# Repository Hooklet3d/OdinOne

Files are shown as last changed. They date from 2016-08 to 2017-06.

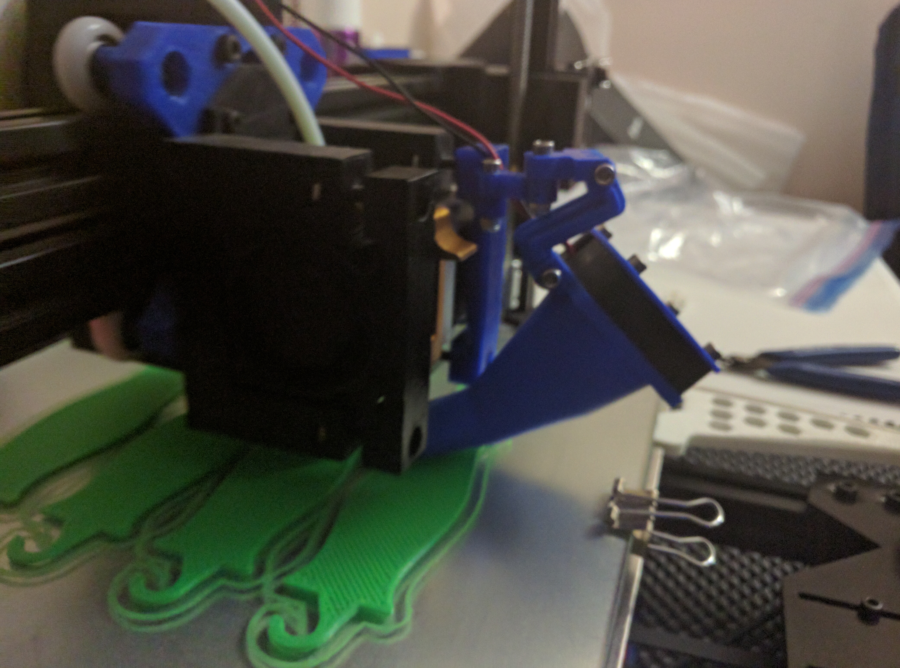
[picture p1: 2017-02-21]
Parts/OdinOne/Mods/Mk1Cooler/LayoutExample2.jpg

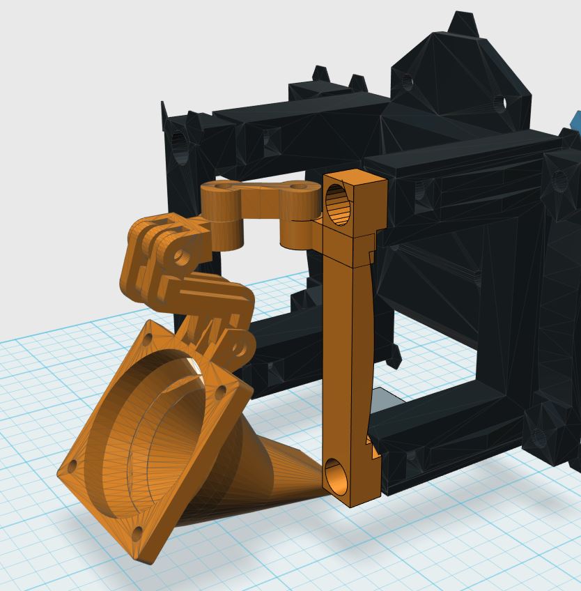
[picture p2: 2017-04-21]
Parts/OdinOne/Mods/Active_Cooling/Mk8CoolerModular/ModLayout.JPG

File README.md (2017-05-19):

# Odin One 3d Printer

Published under GPL v3

## About

This repository contains the files needed to print and assemble the 3d printed parts of the Odin One 3d printer.  As the machine is modified this repository will be updated to reflect the most current revision.  

Each folder contains a text file with basic information on how to configure and print these parts.  Please reference the build manual for specific information on assembly.  

A primary goal of the Odin One is the create a high quality teaching tool.  Contributing to 3d printing eduction for the public is very important to us.  With that said, please share your contributions and findings with the community. 

## What's New

## May 2017

* Work continues on improving the included cooling solution (duct), currently the duct is effective but we do have some room to improve.  
* The team is focusing on producing kits and as we move into the summer show tour
* It's time to start looking into ways of improving the extruder solution and the x-axis; a key point of improvement is weight reduction.
* We are looking at making big improvements to the MK8 extruder as well, more on that to come!
* The current controller case solution is being updated and improved as of now. 

### May 19 2017

PR: Mercury 1 (PR#66)
*	Reworked Unicap’s to tighten tolerances and reduce weight
*	Fixed an alignment issue with the Bed Belt Mount
*	Reworked Y Idle Mount
*	Reworked Y NEMA Mount for better fit
*	Reworked MK8 Mount for better alignment and strength 

#### April 2017
All MK1 parts have been uploaded to the master branch.
The WIKI is slowly being updated with info and specific guides

### What's Next

Moving forward we will be focusing on improving documentation (to include BOM) and including CAD files for all parts.

Currectly the Odin CAD files are SKP (Sketchup) we will be reworking and sharing Fusion360 files for all items.

### TODO

We need to verify and update the documentation (this includes markup on existing .MD files)

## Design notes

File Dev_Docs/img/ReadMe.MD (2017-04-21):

# Docs Needed

## Guide Docs

* Belt Adjust
* Setting Z-Offset

## Build Docs

* Machine Verification
* Fan Wiring

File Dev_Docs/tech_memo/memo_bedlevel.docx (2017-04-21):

Hooklet3D
Odin One Development

Monticello, MN 55362

MEMORANDUM

Date: March 27, 2017

To: Community

From: Hooklet Development Team

Subject: Manual Bed Level

Summary: The Odin One MK1 is equipped with an auto bed level (ABL) system, this does not mean there’s no need to level the bed, however, it does limit the frequency it must be leveled. The addition of the ABL system slightly alters the process of leveling the bed. This document will outline the steps needed to physically level the build surface.

Process:

Step 1-

Tighten the bed thumbscrews compressing the bedsprings to approximately half their extended length

Step 2-

Auto home the machine using either the LCD or Gcode and then perform an auto bed level:

LCD: Prepare/Auto Home

Code: G28;

LCD: Prepare / Level Bed

Code: G29;

Step 3-

Manually move the nozzle so it’s approximately centered over the bed.

LCD: Prepare/Move Axis… X/Y

Code: G1 Xxx Yyy;

Step 4-

Lower the nozzle until a business card (or something similar) barely slides between the nozzle and the bed. There should be some resistance.

LCD: Prepare/Move Axis/ .1/Z

Code: G1 Z-.1;

Step 5- Disable the stepper motors

LCD: Prepare/Disable Steppers

Code: M84;

Step 6-

Move the nozzle and bed by hand positioning the nozzle at each corner and adjusting the thumbscrew at each location so that a business card slides between the nozzle and bed surface.

The resistance at each corner should feel similar, this does not need to be exact (although the closer the better) as we will be correcting the bed with the ABL system.

Comments:

The ABL system will correct for changes in your manual bed level over time, best practice is to manually the bed when print quality begins to suffer, or if you have noticeable issues printing on the entire bed.

The bed level has no impact on the nozzle distance from the bed surface, this is handled by the ABL system; in other words, rising the bed will not cause the nozzle to print closer to the bed, this must be adjusted via the z offset value in the LCD or slicer.

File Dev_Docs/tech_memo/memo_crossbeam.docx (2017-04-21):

Hooklet3D
Odin One Development

Monticello, MN 55362

MEMORANDUM

Date: March 19, 2017

To: Community

From: Hooklet Development Team

Subject: Cross Beam Assembly

Summary – The Cross Beam Assembly is the gantry for the x-axis, this consists of two large 3d printed end caps connecting two 2020 Aluminum Extrusions. These aluminum extrusions provide the linear motion and stabilization for lateral extruder movement.

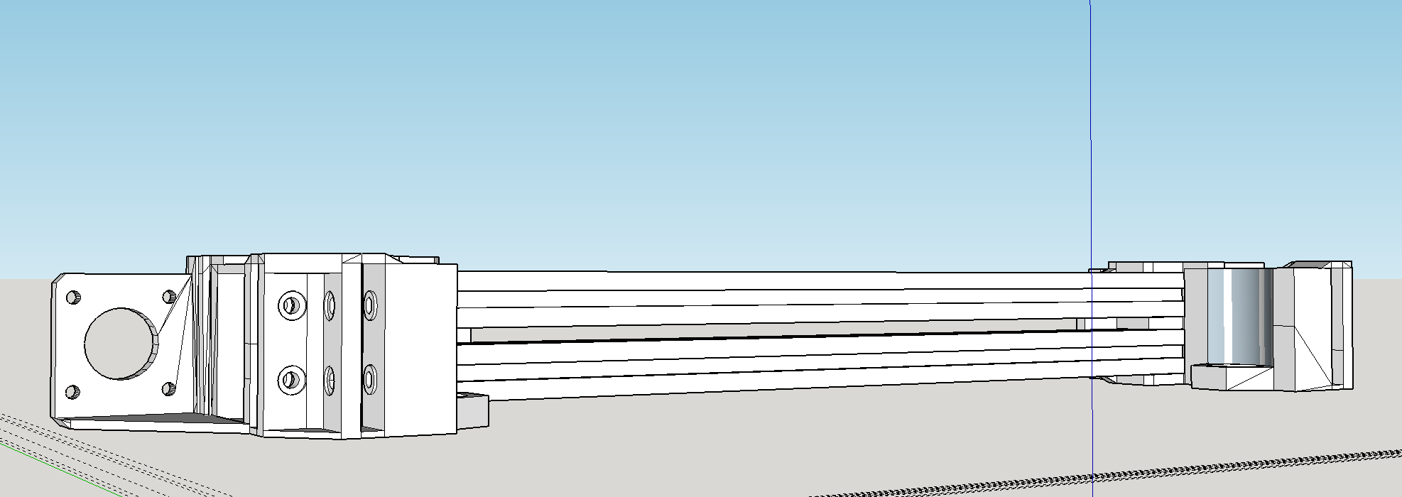
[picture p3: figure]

In addition to movement, the Cross Beam Assembly provides mounting for the motor, drive system, and end-stop for x-axis movement. X-axis movement is driven by a GT2 belt, 16 tooth GT2 idler pulley and a flange bearing set. This open belt system drives the extruder assembly across the x-axis.

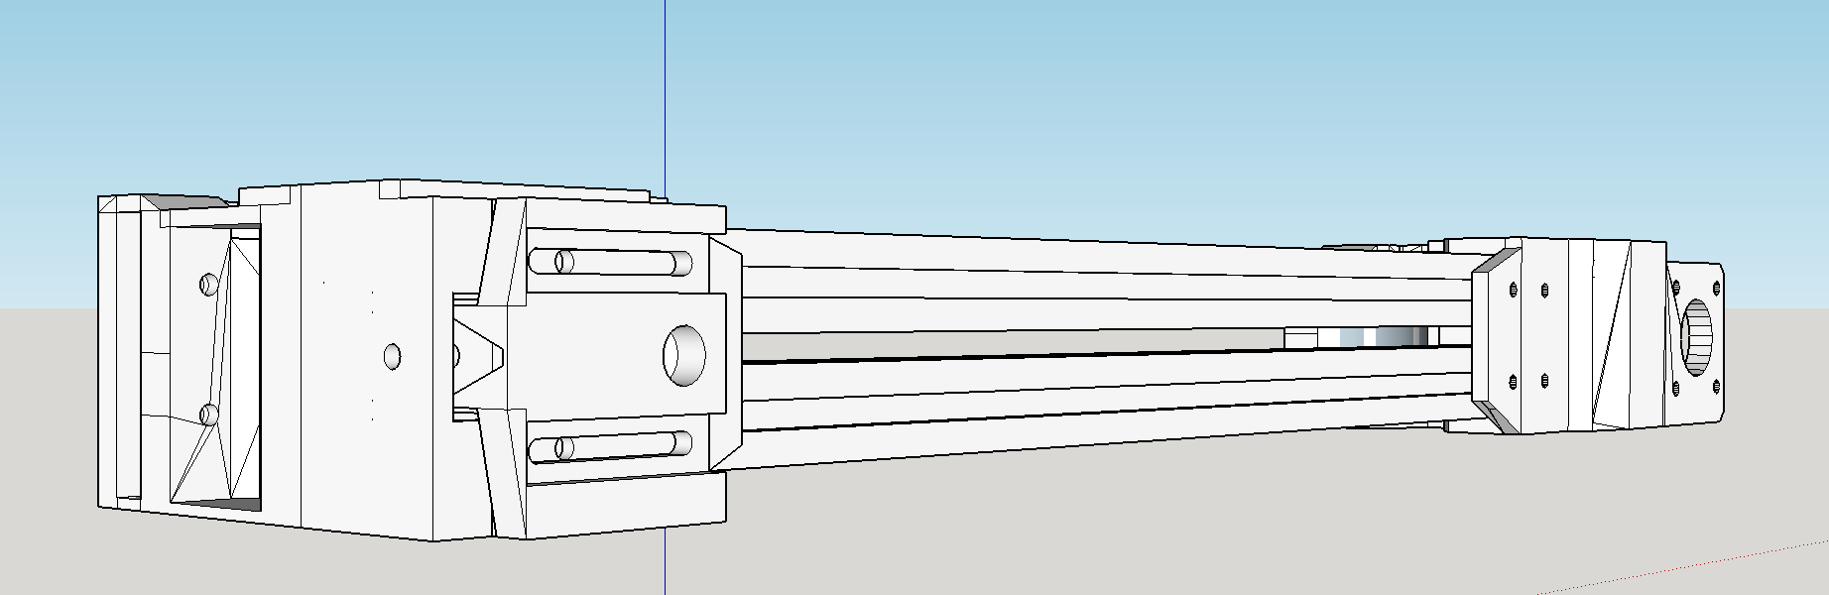
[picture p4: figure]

The end cap parts also house the nut for the z-axis lead screws. The lead screws drive the z-axis along 2020 aluminum uprights. Embedded nylon roller wheels provide smooth movement; the nylon roller wheels do not require lubrication and provide superior longevity and quite movement when compared to conventional thrust bearings.

Printed Parts –

X1 – UnicapIdle

X1 – UnicapNEMA

X1 – X-Idle Face

Notes:

These are the settings Hooklet uses internally; you may need to adjust these to meet your own needs/machine requirements.

All parts printed in PET-G.

UnicapIdle:

Layer | .2mm
Speed | 45mm/s
Infill | 35%
Support | Yes
Temp | Extruder Bed 235c 65c

Notes: The Unicap parts take some time to print, given their size make sure you begin printing with a well-calibrated z-axis.

UnicapNEMA:

Layer | .2mm
Speed | 45mm/s
Infill | 35%
Support | Yes
Temp | Extruder Bed 235c 65c

Notes: The Unicap parts take some time to print, given their size make sure you begin printing with a well-calibrated z-axis.

X-Idle Face

Layer | .2mm
Speed | 45mm/s
Infill | 35%
Support | No
Temp | Extruder Bed 235c 65c

Non-Printed Parts:

Fasteners:

- M3x12
- M3x14
- M4x10
- M5x25 Countersunk
- M4 Hammer Nut
- M3 Nylock
- M5 Nylock

Electronics

- NEMA 17

Other

- GT2 Belt
- X2 Flange Bearing
- Nylon Roller Wheel

Concerns:

Although it’s completely functional as is, it would be beneficial to reduce the weight of the crossbeam. The most logical area to reduce would be the Unicap parts, this would also reduce machine print time and material cost.

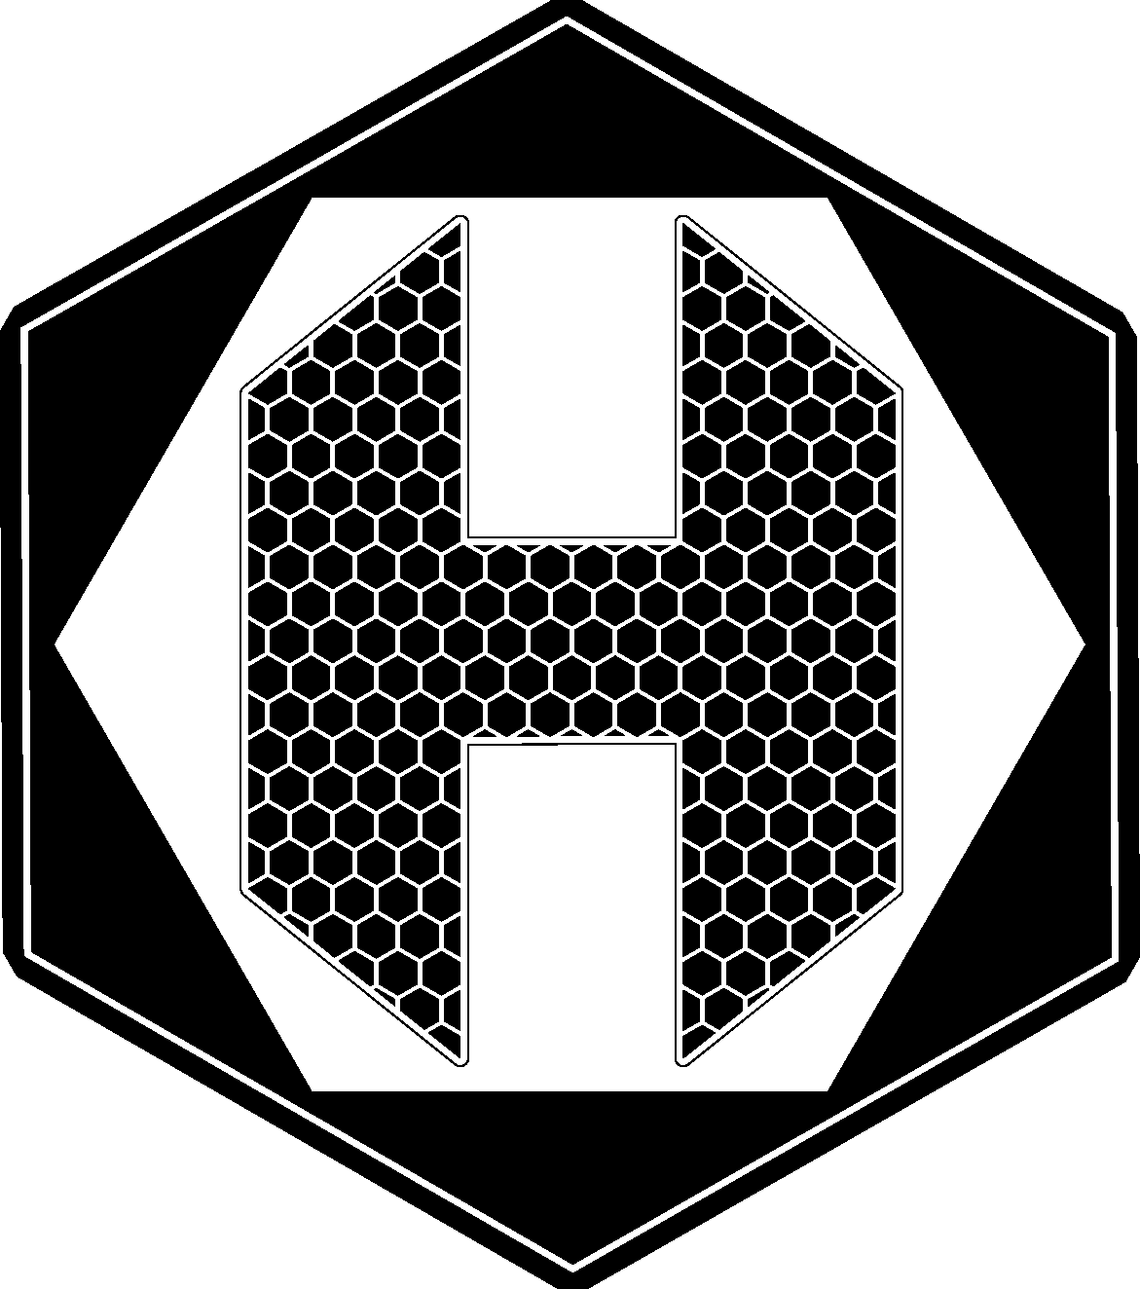
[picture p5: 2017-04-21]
Dev_Docs/img/hooklet.concept4-BLK.png

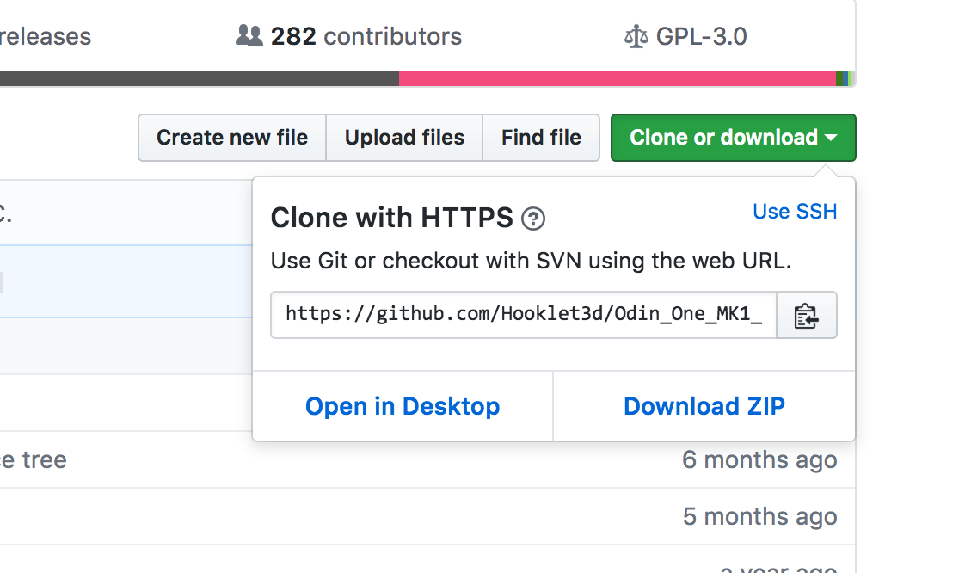
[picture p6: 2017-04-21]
Dev_Docs/img/git_clone_download.png

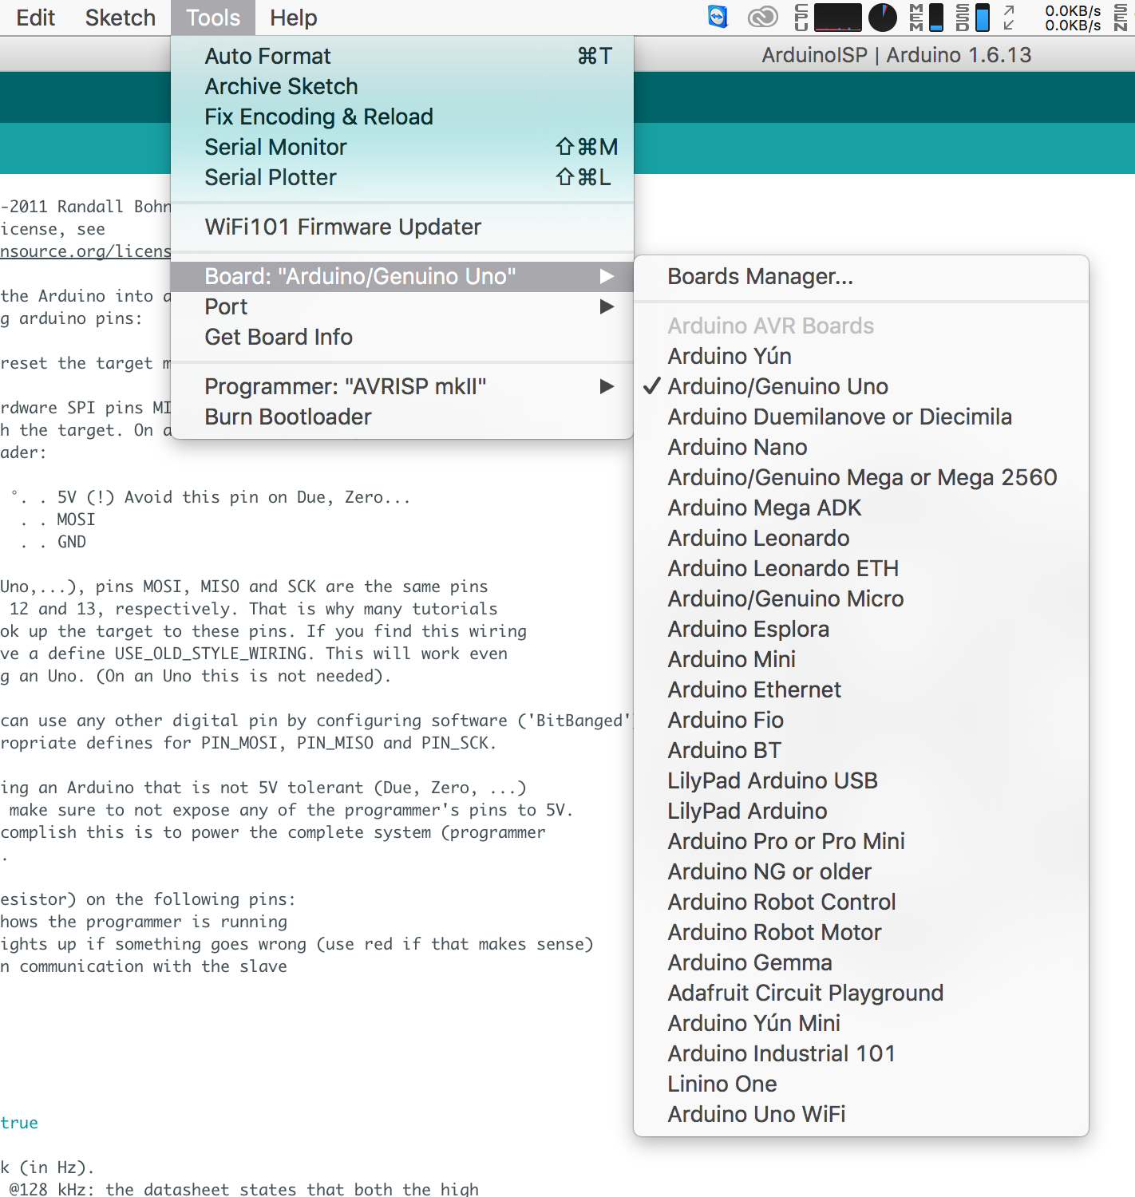
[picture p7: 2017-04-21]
Dev_Docs/img/ard_select_UNO.png

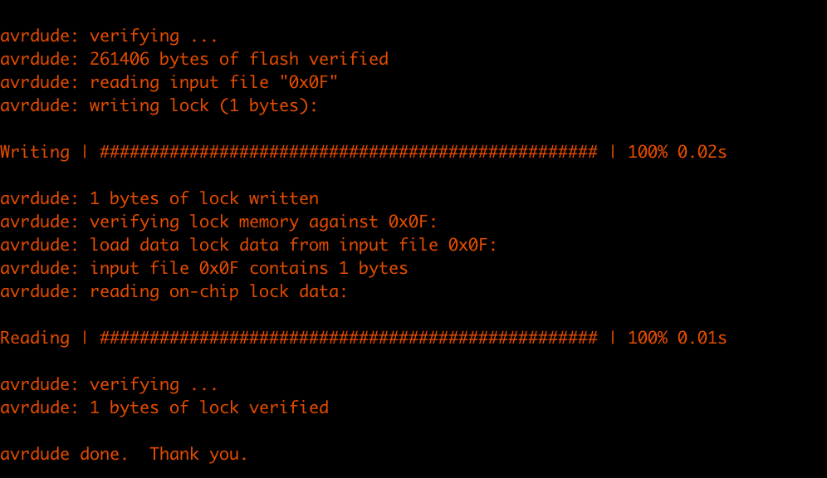
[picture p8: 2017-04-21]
Dev_Docs/img/ard_bootloader_complete.png

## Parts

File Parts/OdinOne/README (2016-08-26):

Printed Parts BOM (notes)

=========================================================
This file outlines the parts needed to print an Odin One, 
here you can find notes on each part and quantity needed
=========================================================

*********************Notes*******************************

The settings below are only recommendations, this may change from printer-to-printer.  Use
these as a starting point and use your best judgement.  These settings were determined in Simplify 3D

All parts are to be printed in ABS... 

*********************************************************

======Frame Start========

-Frame-

-Base Side-
  -Quantity X2
  -Fill 30%
    -Layers-
      Base-2
      Outline-2
      Top -4

Notes:

The base side STL is large, make sure you are printing it on a full 200x200 build space
Depending on how you position the part you will want to make sure your build plate is properly 
aligned to prevent the printer from leaving the printspace.

-Base Front-
  -Quantity X1
    -Fill 40%
      -Layers-
        -Base-2
        -Outline-2
        -Top -4
        
Notes:

The Front STL is to be printed upside down, it has a large surface area so proper heatbed settings should be used to prevent 
warping.  

-Base Rear-
  -Quantity X1
    -Fill 40%
      -Layers-
        -Base-2
        -Outline-2
        -Top -4
        
Notes:

The Rear STL is to be printed upside down, it has a large surface area so proper heatbed settings should be used to prevent 
warping.

-Upper 90 Set-
  -Quantity X1
    -Fill 40%
      -Layers-
        -Base-2
        -Outline-2
        -Top -4
        
Notes:

This STL contains both the right and left upper 90 corners.

-Z Nema Mount-
  -Quantity X2
    -Fill 40%
      -Layers-
        -Base-2
        -Outline-2
        -Top -4
        
======Frame End========
        
Notes:

This part mounts the two Nema steppers to the 2020 uprights.   

-Z EndMount-
  -Quantity X1
    -Fill 40%
      -Layers-
        -Base-2
        -Outline-2
        -Top -4
        
Notes:

This part holds the optical end stop for the z axis.

-X Skate-
  -Quantity X1
    -Fill 40%
      -Layers-
        -Base-2
        -Outline-2
        -Top -4
        
Notes:

This part holds nylon roller wheels and provides movement on the X axis.  It also serves as the mounting point for the 
Odin's effector head.

-Skate-
  -Quantity X4
    -Fill 40%
      -Layers-
        -Base-2
        -Outline-2
        -Top -4
        
Notes:

This part holds nylon roller wheels and provides movement for the Z and Y axis.  The skate also includes optional preload adjustment.  

-Z Beam Set-
  -Quantity X1
    -Fill 40%
      -Layers-
        -Base-2
        -Outline-2
        -Top -4
        
Notes:

This part Joins the horizontal beam of the Odin One, the print includes the parts for both ends.  Depending on the accuracy of your 
machine, you may need to adjust the placement of the part when constructing the printer.  

-Y Nema Mount-
  -Quantity X1
    -Fill 40%
      -Layers-
        -Base-2
        -Outline-2
        -Top -4
        
Notes:

This part connects the Y Nema motor to the 'Base Rear' part of the Odin One.  It has been made its own part to 
Make the building process easier.  

-Y End Mount-
  -Quantity X1
    -Fill 40%
      -Layers-
        -Base-2
        -Outline-2
        -Top -4
        
Notes:

This part holds the optical end stop for the y axis.  It is located under the print bed and aligns the endstop with the end tripper.

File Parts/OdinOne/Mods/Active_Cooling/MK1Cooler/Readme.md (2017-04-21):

##MK1 Active Cooler 

**Must be printed with supports**

The MK1 Active Cooler mounts onto the rear of the MK8 Odin Mount.  It uses existing hardware and requires no additional modificaton.

The MK1 is designed to be fitted with a 40mm fan. 

###Fan selection and use... 

The fan you use should be a 12v fan, this fan will be attatched to the MK1 Cooler and by design must be positioned to push air vs pull.  

The fan should be wired to the existing 'Fan' connection on your Odin's control board.  This connection is found on the blue rail that 
contains the connections for the bed and extruder.  

Once the fan is attatched you will be able to access and use it via your slicer or Gcode commands.  

_Note:  Add the following to your starting script:_

```
M107; Turn fan off...
```
This will make sure the fan is off prior to starting warm-up.  Running the fan while warming up can cause issues with heating.

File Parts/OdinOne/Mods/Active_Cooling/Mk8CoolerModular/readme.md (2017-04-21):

Modular Mk8 Cooling mod files

----------------

All parts printed in ABS;

Layer height: 0.2mm;

Top Layers: 4;

Bottom Layers: 4;

Walls: 3;

Infill: 35%;

Supports: no;

Print time: approx 3 hrs

------------------

Custom modified version of: http://www.thingiverse.com/thing:540716

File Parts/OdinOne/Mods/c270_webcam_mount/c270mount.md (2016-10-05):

This is a modular adjustable Webcam mount for the Logitech c270.

Camera mount will require removal of the webcam's mount by removing the rubber screw covers, removing the screw and carefully removing the rod & bushing for reuse.

I also removed the front faceplate from mine so as to access the manual focus.

The middle sections are a smaller version of these: Cable Organizer the included file is already sized to work with this system.

I created a custom mount for my Hooklet 3D Odin One reprap printer, but I also included a generic base aswell.

0.2mm
30% Infill
No supports.

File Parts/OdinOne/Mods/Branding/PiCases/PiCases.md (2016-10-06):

Cases for Raspberry Pi with Fan mounts & Hooklet 3D logos.

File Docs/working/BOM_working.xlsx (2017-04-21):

Fasteners
Part | Quantity
M3
M3x8 | 18
M3X12 | 30
M3x16 | 2
M3x30 | 4
M3x40 | 2
M4
M4x10 | 59
M4x25 | 6
M4x40 | 2
M5
M5x25 Counter | 29
Nuts
M3 Nylock | 26
M5 Nylock | 29
M4 Hammer | 61
M6 Jam Jut | 2
Thumb Screw | 4
Frame
2020 x 400 Extrusion | 9
Bed Spring | 4
Motion
GT2 Pulley 16 tooth | 2
Worm Coupling | 2
GT2 Belt | 1
8mm Worm Gear | 2
Bed Platform | 1
8mm Worm Nut | 2
Nylon Roller Wheel | 26
Electronics
NEMA 17 40mm | 5
Opto End Stop | 3
DRV Stepper Driver | 4
Heated Build Plate | 1
40mm Fan | 1
Thermistor | 2
Heating Element | 1
LCD Set | 1
PSU 12v 240w | 1
2in1 Board | 1
Heatsink | 1
PEI Bed Surface | 1
MK8 KIT | 1
Thermal Break 6mm | 1
Nozzle .4mm | 1

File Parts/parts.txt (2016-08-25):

Parts

This folder contains the master parts bill for all Odin iterations.  New branches, modifications or other changes should
be placed in thier own respective folders.  For example, a modification for the Odin One named 'new spool' should have the following path:

Odin/Parts/OdinOne/Mods/newSpool

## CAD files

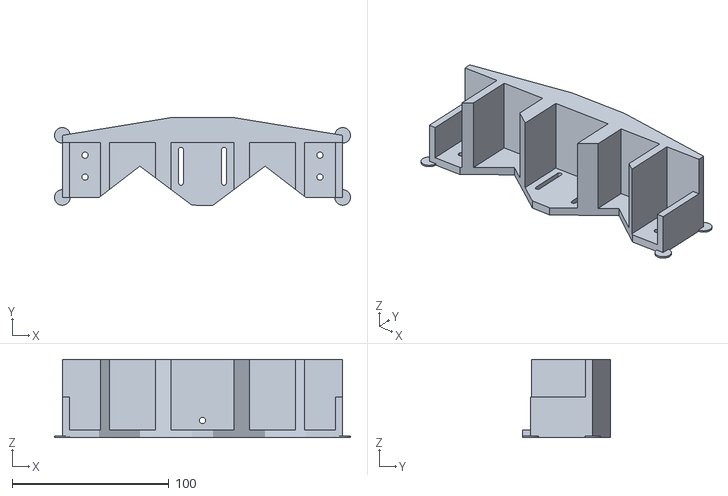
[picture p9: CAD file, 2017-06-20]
Parts/OdinOne/Frame/Base_Front_MK1.stl
189.0 x 56.1 x 50.0

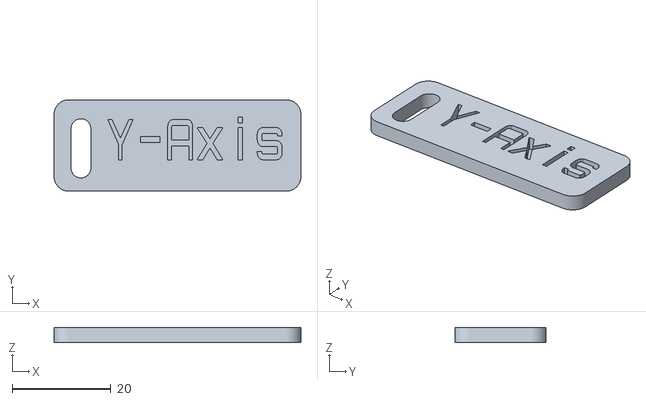
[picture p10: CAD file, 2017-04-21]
Parts/OdinOne/Mods/acc/lab_y_axis.stl
50.1 x 18.5 x 3.00

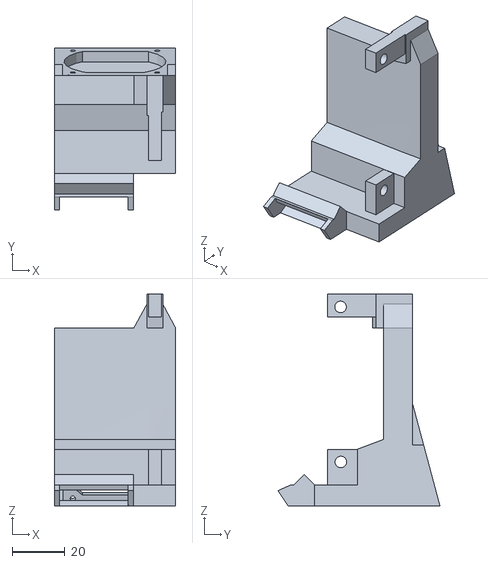
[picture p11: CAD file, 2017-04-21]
Parts/OdinOne/Mods/Active_Cooling/MK1Cooler/NewMK8FanShroud.stl
46.0 x 61.4 x 80.4

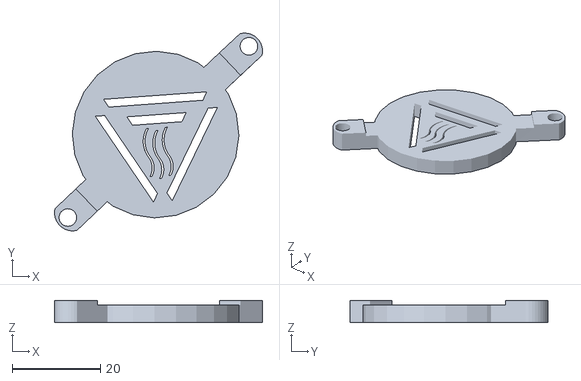
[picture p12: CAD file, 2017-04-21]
Parts/OdinOne/Mods/Active_Cooling/MK8_DraftCooler/Fan_Guard_DraftCoolerMK8.stl
47.2 x 44.8 x 5.00

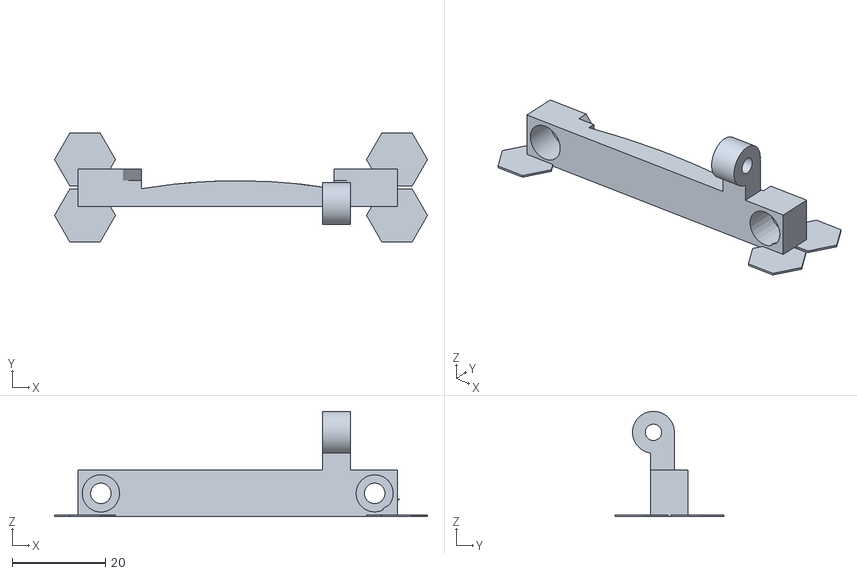
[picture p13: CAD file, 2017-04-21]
Parts/OdinOne/Mods/Active_Cooling/Mk8CoolerModular/MountMod_1.2.stl
80.1 x 23.4 x 22.6

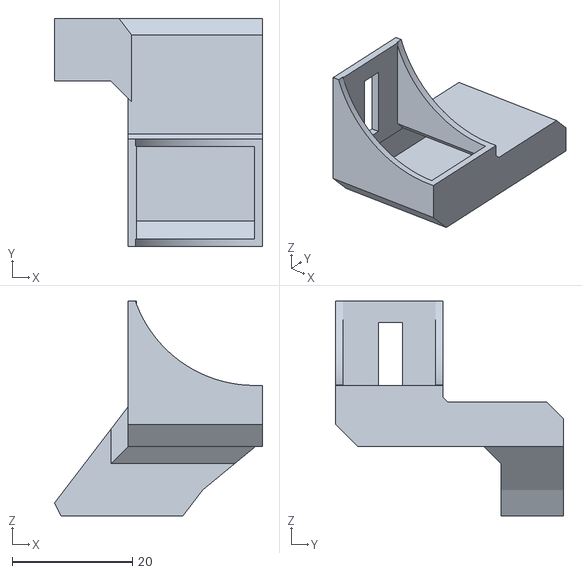
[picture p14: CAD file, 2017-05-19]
Parts/OdinOne/Mods/Active_Cooling/Straight_Duct/MK1.1BlowerMod_STRAIGHT.V5b.stl
34.6 x 37.9 x 35.7

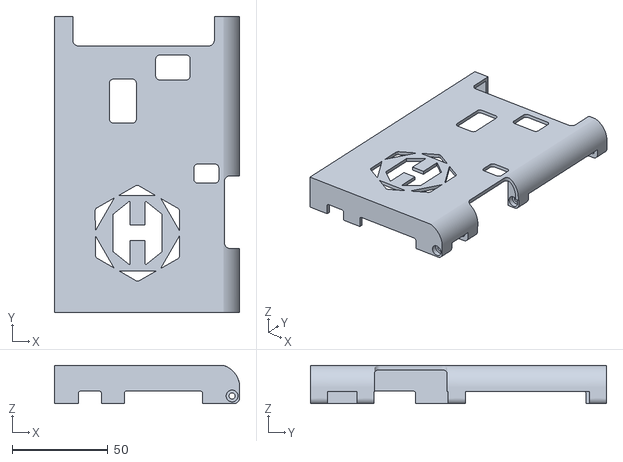
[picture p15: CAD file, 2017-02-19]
Parts/OdinOne/Mods/BrainBoard/BrainBoardCover.v3.stl
97.0 x 154.8 x 20.0

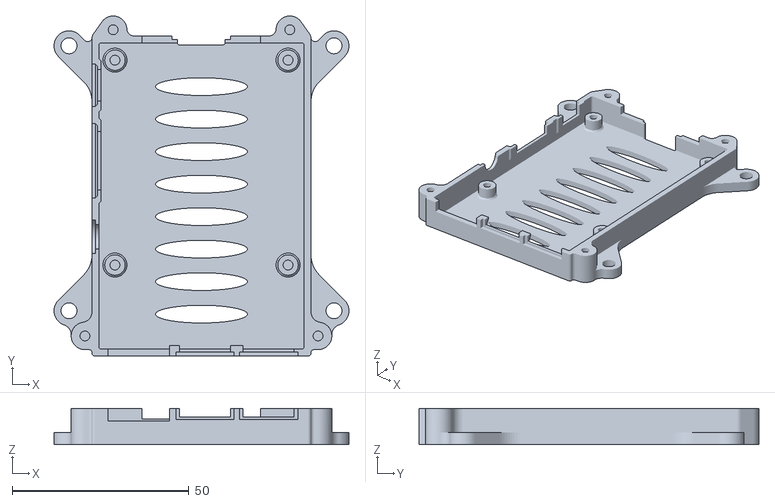
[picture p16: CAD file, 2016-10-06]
Parts/OdinOne/Mods/Branding/PiCases/rpi3-bottom_netfabb.stl
83.5 x 96.2 x 10.3

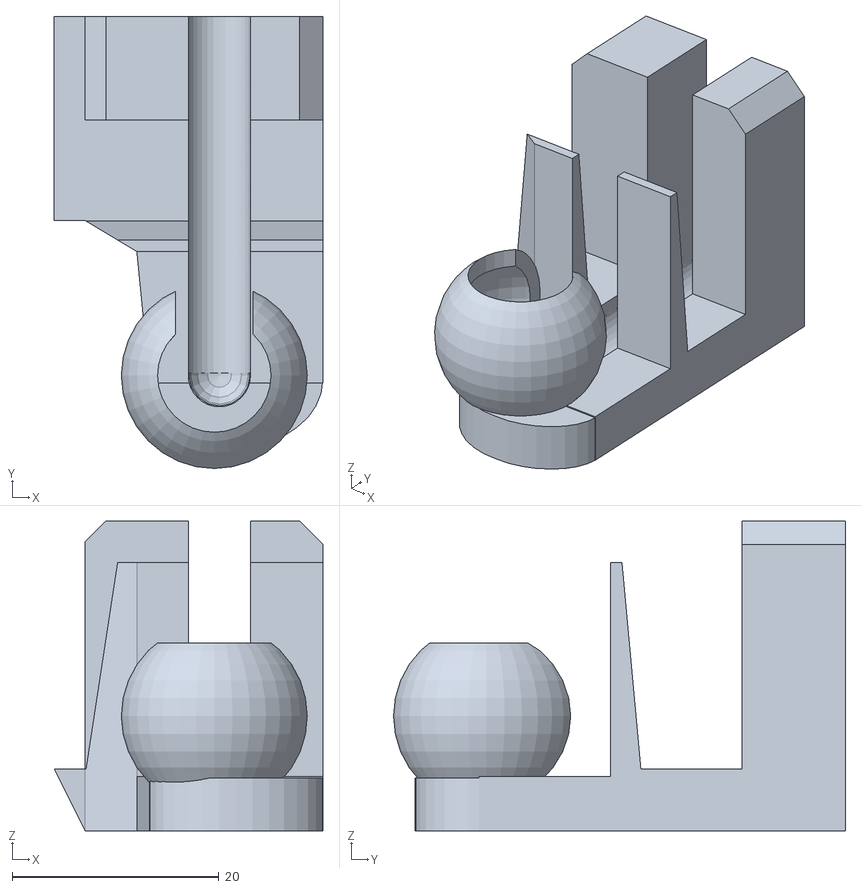
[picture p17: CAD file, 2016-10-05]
Parts/OdinOne/Mods/c270_webcam_mount/odin_front_adapter_fixed.stl
26.0 x 43.8 x 30.0

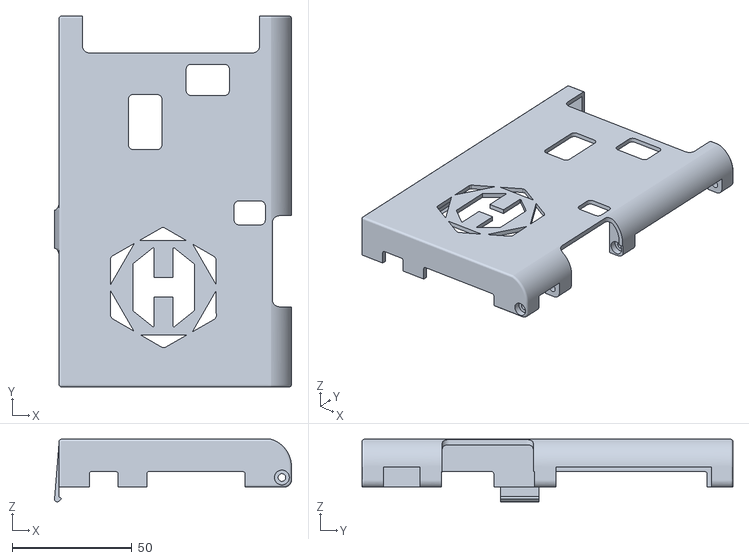
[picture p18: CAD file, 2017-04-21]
Parts/OdinOne/Mods/Controller_Mount/ControllerBoardCover.v4.stl
98.9 x 154.8 x 26.2

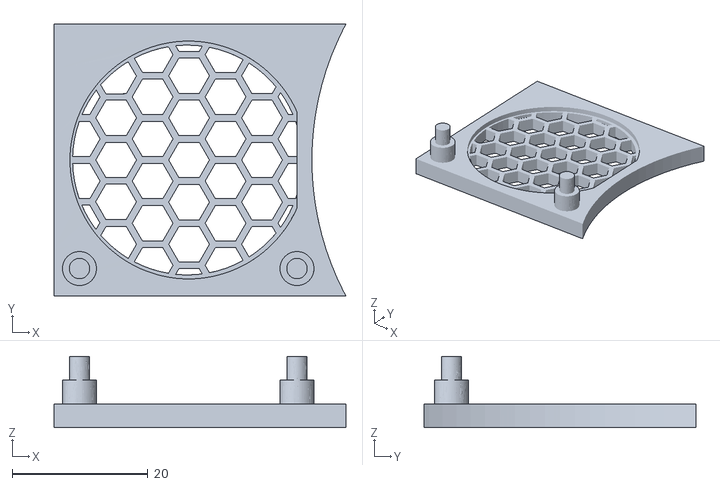
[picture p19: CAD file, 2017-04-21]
Parts/OdinOne/Mods/Guards /FanGuard_Hex.stl
43.0 x 40.0 x 10.5

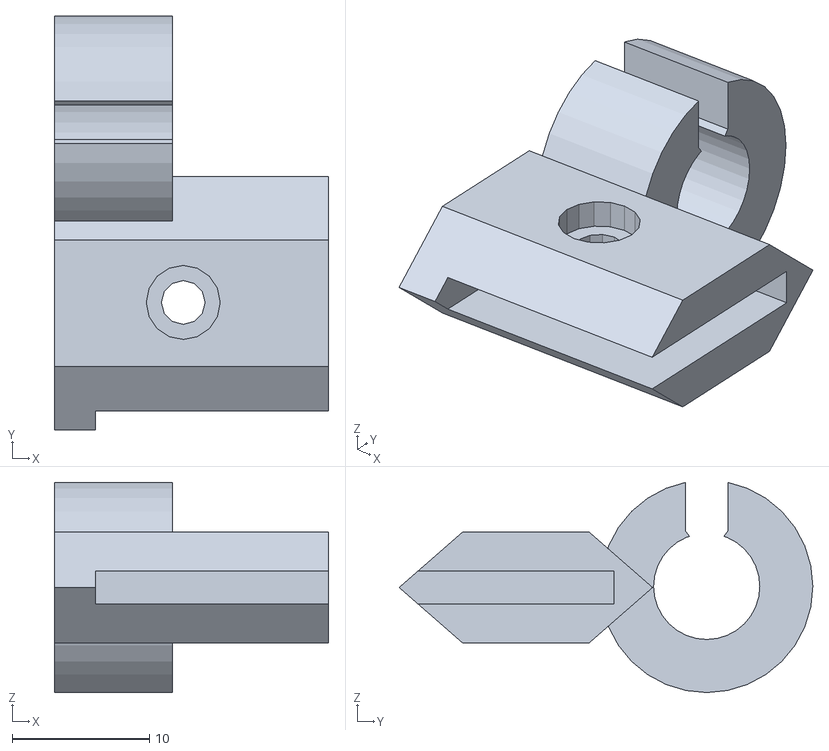
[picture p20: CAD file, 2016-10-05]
Parts/OdinOne/Mods/heatedbed_wireclamp.stl
20.0 x 30.2 x 15.3

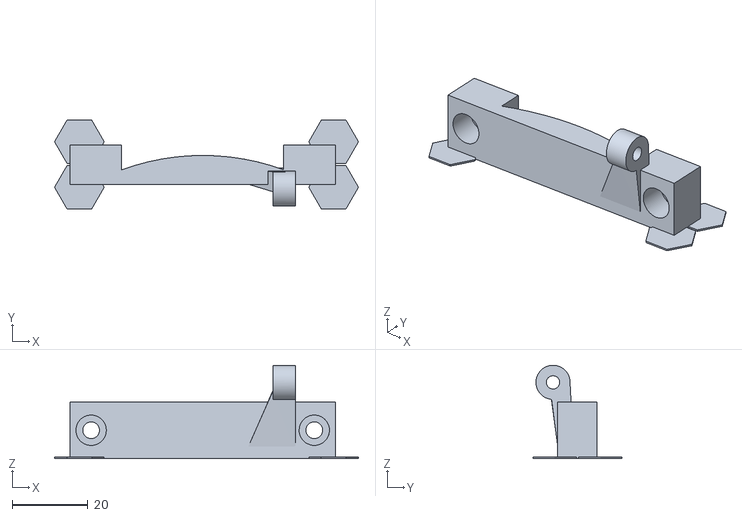
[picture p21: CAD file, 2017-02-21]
Parts/OdinOne/Mods/Mk1Cooler/MK1Strap.v2.stl
80.1 x 23.4 x 24.6

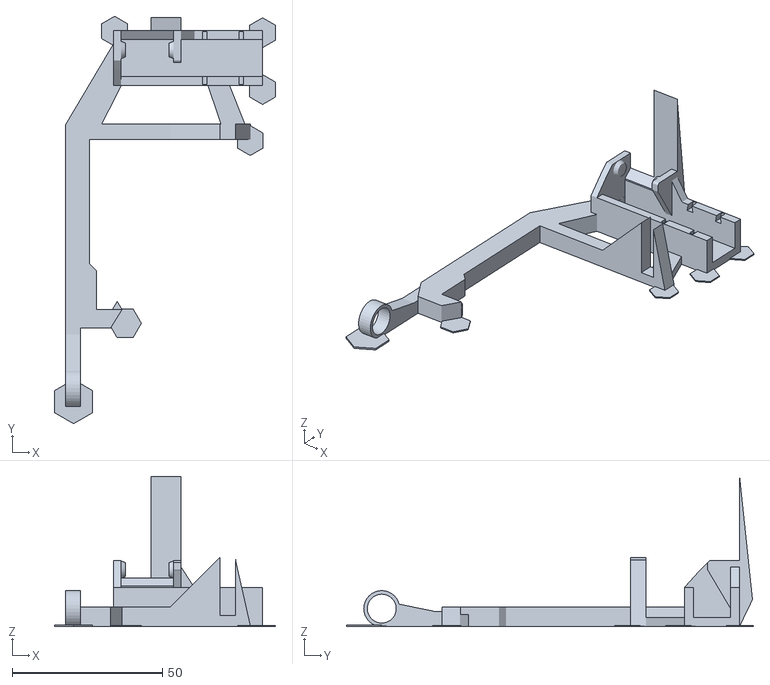
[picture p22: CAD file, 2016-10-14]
Parts/OdinOne/Mods/WireChain/xbeltextender_chain_adapter_filamentguide.stl
73.5 x 135.5 x 50.0

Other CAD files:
Parts/OdinOne/Mounting/Case_Top_MK1.stl
Parts/OdinOne/Mounting/ExtruderMounts/MK8_MK1/MK8_BackStrap_MK1.stl
Parts/OdinOne/Mounting/ExtruderMounts/MK8_Strap_MK1.stl
Parts/OdinOne/Movement/XIdle_Back_MK1.stl
Parts/OdinOne/Frame/Base_Mid_MK1.stl
Parts/OdinOne/Frame/Base_Rear_MK1.stl
Parts/OdinOne/Frame/Base_Side_MK1.stl
Parts/OdinOne/Frame/Upper90_Front_SET_MK1.stl
Parts/OdinOne/Frame/Upper90_Rear_SET_MK1.stl
Parts/OdinOne/Mods/Active_Cooling/MK8_DraftCooler/Fan_Duct_DraftCoolerMK8.stl
Parts/OdinOne/Mods/Active_Cooling/MK8_DraftCooler/Fan_Mount_DraftCoolerMK8.stl
Parts/OdinOne/Mods/Active_Cooling/Mk8CoolerModular/arm1_z_shape_1a.stl
Parts/OdinOne/Mods/Active_Cooling/Mk8CoolerModular/fan_cover_branded.stl
Parts/OdinOne/Mods/Active_Cooling/Mk8CoolerModular/pivot_hinge1.stl
Parts/OdinOne/Mods/Active_Cooling/Mk8CoolerModular/pivot_joint1.stl
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

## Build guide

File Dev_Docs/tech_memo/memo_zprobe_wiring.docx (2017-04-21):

Hooklet3D
Odin One Development

Monticello, MN 55362

MEMORANDUM

Date: March 27, 2017

To: Community

From: Hooklet Development Team

Subject: Z Probe Wiring

Summary:

The Z Probe used for the MK1 ABL system requires a voltage divider to function properly. This document outlines the procedure for wiring the Z Probe.

Background:

The Z Probe has 3 main wires (signal, ground, 12v) these wires are unfinished, to finish the z probe we need to add two resistors and DuPont connectors.

One of these wires connects to an available 12v auxiliary output on the control board and the other two are connected to the z min end stop’s signal and ground pins.

Wiring:

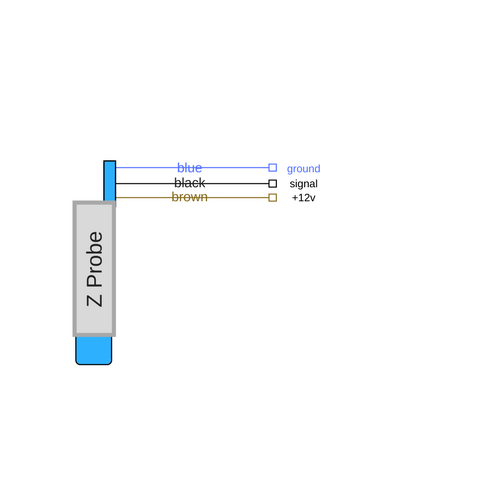
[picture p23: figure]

Be aware of the color-coding of the probe wires, as it is possible to damage the board by reversing any of these wires.

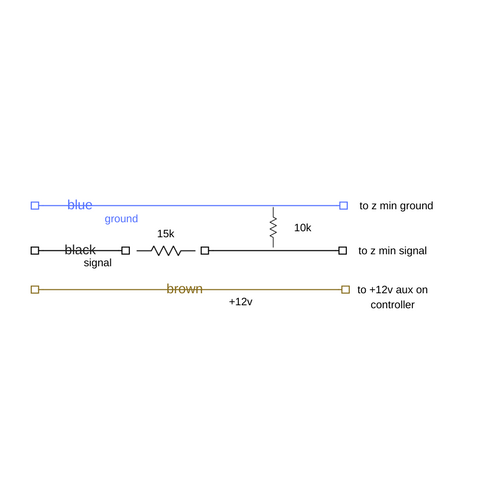
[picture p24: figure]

To create the voltage divider, we place a 15k resistor on the signal line (in line) and then bridge the signal line to the ground line using a 10k resistor.

The 12v power is run directly to the auxiliary pin of the control board.

Connecting

The signal and ground wires are terminated to a 2 pin female DuPont connector and connected to the Z Min pins (signal and ground). Do not connect this to the 5v (third) pin on the Z Min pin out.

The 12v power is terminated to a single pin female DuPont connection and plugged into an available 12v auxiliary pin.

Notes:

Make sure all wires and splices are covered using electrical tape, shrink-wrap or both. It is very important that these do not short.

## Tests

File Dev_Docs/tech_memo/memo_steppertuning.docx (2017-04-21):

Hooklet3D
Odin One Development

Monticello, MN 55362

MEMORANDUM

Date: March 27, 2017

To: Community

From: Hooklet Development Team

Subject: Stepper Tuning

Summary:

The drivers for the stepper motors must be tuned to provide the correct output amperage to the stepper motors. The Odin One uses DRV8825 Stepper Drivers; these stepper drivers produce a max output of 2.2amps per coil.

The output is adjusted using a potentiometer located on the top of the Stepper Driver. Using a multimeter you can read the stepper driver’s reference voltage by placing the meters positive probe on the potentiometer. Be sure the black probe is grounded prior to doing this; not doing so will destroy the stepper driver.

The conversion for DRV8825 reference voltage to output amps is simple; the reference voltage is equal to half the output amps.

So, if the reference voltage reads at .50v, the output amperage is 1amp.

The Odin One’s stepper motors are rated at a max of 1.2amps.

So, to tune the drivers to produce at the maximum rated capacity of the stepper motors, we would want to set the reference voltage to .60v.

The Z axis has two motors sharing a single driver, this driver must be set to produce twice the output amperage.

Note: The max output of the DRV8825 is 2.2amps, so we cannot produce the max load of the combined Z motors @2.4amps instead we operate at the upper limit of the driver.

Setting VRef:

Using the tip of the multimeter (while grounded) gently turn the potentiometer observing the voltage as you go. The target values for each axis are outlined below.

Axis | Operational Range | Max Setting | Output Amps
X | 0.40 - 0.60v | 0.62v | 1.2amps @0.6v
Y | 0.40 - 0.60v | 0.62v | 1.2amps @0.6v
Z | 1.00 - 1.10v | 1.10v | 2.2amps @1.1v
E | 0.50 - 0.60v | 0.62v | 1.2amps @0.6v

We can account for a .05 margin of error on all axis, however, running a higher rates increases the risk of thermal failure and may limit the life of the stepper driver.

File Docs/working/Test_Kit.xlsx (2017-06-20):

Test | Result
Movement | PASS
End-stops | PASS
Z-Probe | PASS
Probe Accuracy | 0.003221
Heat Extruder | PASS
Heat Bed | PASS
Print Test | PASS
USB Print | PASS
SD Print | PASS
Factory Z-Offset | -0.31
OD-MK1-1006
Test | Result
Movement | PASS
End-stops | PASS
Z-Probe | PASS
Probe Accuracy | 0.003221
Heat Extruder | PASS
Heat Bed | PASS
Print Test | PASS
USB Print | PASS
SD Print | PASS
Factory Z-Offset | -0.12
OD-MK1-1007
Test | Result
Movement | PASS
End-stops | PASS
Z-Probe | PASS
Probe Accuracy | 0.003242
Heat Extruder | PASS
Heat Bed | PASS
Print Test | PASS
USB Print | PASS
SD Print | PASS
Factory Z-Offset | -0.32
OD-MK1-1008
Test | Result
Movement | PASS
End-stops | PASS
Z-Probe | PASS
Probe Accuracy | 0.009521
Heat Extruder | PASS
Heat Bed | PASS
Print Test | PASS
USB Print | PASS
SD Print | PASS
Factory Z-Offset | -0.91

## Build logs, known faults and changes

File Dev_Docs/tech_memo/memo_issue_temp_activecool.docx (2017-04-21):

Hooklet3D
Odin One Development

Monticello, MN 55362

MEMORANDUM

Date: March 27, 2017

To: Community

From: Hooklet Development Team

Subject: Temperature fluctuations due to active cooling.

Summary:

In routine testing it was shown that wide ranging temperature fluctuations to include a failure to heat could be caused by an incorrectly installed active cooler. In this case the issue triggered the Thermal Runaway failsafe.

Background:

A failure was induced that resulted in the thermal protection system halting the machine upon activation of the active cooling fan. During observation, it was shown that upon activation of active cooling the primary extruder reduced its temp from its current set point to approximately 20c below set point. The sustained lowered temperature triggers the thermal runaway failsafe.

This implies a lack of current to the primary extruder, which would prevent the heater from reaching its full output. In this case we know our input voltage remained static, and also that the standard load of a 12v active cooling fan is not beyond the threshold of our power supply.

The failure is due to a loose connection. Given we use cable terminators, it is possible to under tighten these connections without notice.

Test Conditions

This failure was created by intentionally loosening the active cooling fan’s positive connection to the control board. This loose connection resulted in additional power draw as well as heat (resistance) at the Fan connection. This was enough to effectively limit the output of the primary heater.

Although the bed is also affected, its thermal mass and ability to maintain a smooth thermal profile prevents it from triggering any failsafe or exhibiting any abnormal behavior.

Impact

This issue will most likely trigger a thermal protection failsafe. It isn’t always immediately obvious as best practices involve not enabling the fan until several layers into the print. In this case the printer will appear to perform fine until the fan is enabled. The user may return to a machine that has been halted and is displaying a thermal error message.

This issue should be a consideration when handling any reported thermal runaway issues. Verification process should include first determining what type of termination the wire has, and then ensuring it is tight.

Solution

Ensure all connections are tight, especially those delivering power from the 12v rail. This will always be the most likely cause of thermal problems.

This may also be inaccurately identified as being the result of the cooling fan blowing on the extruder itself.

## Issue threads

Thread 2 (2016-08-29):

YEndMount Fix

3dGriff, 2016-08-29:
The mount for the Y end stop needs to be adjusted to allow better clearance.  In some cases the Bed skate wheel hits the front of the mount preventing it from tripping the optical end stop.

3dGriff, 2016-09-29:
File uploaded

Closed 2016-09-29.

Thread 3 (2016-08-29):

Y Belt Mount Adjust

3dGriff, 2016-08-29:
Remove -2mm from base vert and 3mm from top vert to allow the use of M3X25mm bolts.

3dGriff, 2016-09-29:
Fixed/updated

Closed 2016-09-29.

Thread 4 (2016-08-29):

Y Tripper

3dGriff, 2016-08-29:
Overhang on tripper prevents smooth movement of bed skate system

3dGriff, 2016-09-03:
Adjusted and uploaded, issue closed.

Closed 2016-09-03.

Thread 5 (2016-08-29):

Y Nema Mount adjust

3dGriff, 2016-08-29:
The Y Nema mount needs to be adjusted to fit the larger NEMA motors.

3dGriff, 2016-09-29:
Fixed and updated.

Closed 2016-09-29.

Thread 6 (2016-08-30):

End Beam Fix

3dGriff, 2016-08-30:
The End Beam Set Has redundant holes that can be removed in the center.

3dGriff, 2016-09-02:
Waiting to test X dim accuracy.  Will update

3dGriff, 2016-09-28:
Issue solved, updating in process.

Closed 2016-09-29.

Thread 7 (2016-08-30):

PSU mounting problem

3dGriff, 2016-08-30:
The M4x10 bolts are not long enough, request adjusting to make it easier to assemble.

3dGriff, 2016-09-28:
Mounts adjusted to allow M4x10 to clear.  Extra consideration must be taken with this part to avoid warping as this seems to be contributing factor.

Closed 2016-09-28.

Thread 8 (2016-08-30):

Y Tripper Offset

3dGriff, 2016-08-30:
The Y tripper needs to be moved about 2mm toward the 2020

3dGriff, 2016-09-03:
Adjusted and uploaded, issue closed.

Closed 2016-09-03.

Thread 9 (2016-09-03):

X Idler Adjust

3dGriff, 2016-09-03:
Shorten bearing shaft 1 mm for clearance.

Bevel washer set for fit.

3dGriff, 2016-09-28:
updated and tested

Closed 2016-09-28.

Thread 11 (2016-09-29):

New Z Tripper

3dGriff, 2016-09-29:
-5mm Adjust to Z Tripper Flag.  Clearance for new Z Skate Mounts.

3dGriff, 2016-09-29:
Uploaded/Closed

Closed 2016-09-29.

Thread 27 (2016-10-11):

X Idle Set Broken

3dGriff, 2016-10-11:
X Idle needs repair.

BotleHewer, 2016-10-14:
STL has been cleaned up to solve slicing issues.

Closed 2016-10-14.

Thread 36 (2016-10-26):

Z Endstop Rework Needed

3dGriff, 2016-10-26:
The Z end stop needs to be adjusted so that the 2020 fastening bolt may be accessed from the front of the machine.  This will allow for easier Z Level adjustment.

Additionally, due to the DuPont connection being loose, we need to add a channel that fits and holds the DuPont sleeve in place and prevents unwanted loosening.

BotleHewer, 2016-11-22:
Reworked File uploaded

Closed 2017-02-16.

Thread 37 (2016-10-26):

X Endstop Rework Needed.

3dGriff, 2016-10-26:
The X Endstop will be reworked to include a sleeve to secure the Dupont connection.

BotleHewer, 2016-11-22:
Reworked file uploaded

Closed 2017-02-16.

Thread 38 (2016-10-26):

Y Endstop Rework Needed

3dGriff, 2016-10-26:
Y Endstop will be reworked to include a sleeve to secure the DuPont connection.

Additionally, the Y Endstop Mount has been cracking near the 2020 fastening bolt when users are tightening the part.  This needs to be reworked.

BotleHewer, 2016-11-22:
Reworked file uploaded.

Closed 2017-02-16.

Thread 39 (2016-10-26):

Endcap reworks.

3dGriff, 2016-10-26:
Due to user feedback the end assemblies will be updated for ease of assembly and machine quality.

The update involves the consolidation of several parts and has been named the UnoEnd_Idle and UnoEnd_NEMA parts respectively.

Closed 2017-02-16.

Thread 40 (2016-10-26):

Base Side Rework

3dGriff, 2016-10-26:
The Base side assembly will be reworked and two additional 2020 extrusions will be integrated into the build.

This will increase the overall stability of the upright section of the machine as well as increase print success rate during production.

Closed 2017-02-16.

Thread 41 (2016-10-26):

LCD case replacement

3dGriff, 2016-10-26:
The current LCD solution is 'soup'

The production model is moving to a different LCD display due to compatibility.  This new display needs a case.

3dGriff, 2016-10-26:
http://reprap.org/wiki/RepRapDiscount_Smart_Controller

The above link is the target display type

Closed 2017-02-16.

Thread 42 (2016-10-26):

Base Front Rework for LCD solution

3dGriff, 2016-10-26:
The Base Front must be reworked for the new LCD mount.

Closed 2017-02-16.

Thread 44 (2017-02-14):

Board mount needs verification

3dGriff, 2017-02-14:
The board mount solution needs to be verified for dimensional accuracy.  Will test and update.

3dGriff, 2017-02-16:
Base dimensional accuracy check complete:

Adjustment needed to fastener holes, not enough clearance for M3x8mm bolts.

_will update and link PR when cover completes_

3dGriff, 2017-02-16:
Cover:

Model needs to be reworked for slicing.

When modeling smooth curves for 3d printing the curve needs a defined break point for proper slicing.  Without this break point the slicer cannot accurately define consecutive layers of the (upward) curve.

In this case the slicer generates a false overhang causing infill to be printed in air.

I have included a screen cap for reference.  Note the yellow tool paths are infill moves.

_currently retesting print with slicer defined (part) z offset -.2 to eliminate first layer as a work [around_]

Note:  This effect can be eliminated by adjusting your extrusion width in the slicer.  This is likely why you did not notice prior to upload.  For repeatability we should repair the issue now.  I was previously unaware of this specific issue with curves, we might want to look into it deeper and share our findings.

I have a feeling based on the slice dimensions and tool paths that this could produce less obvious issues with the print impacting both the end quality and success rate for curved models.

From a more technical standpoint it's worth mentioning that bridging manipulators do not get assigned to infill tool paths.  The test machine is running the Odin Mesh Auto Bed Level, the following are functions of the ABL that likely impact this issue:

- ABL dynamically adjusts Z height based on the correction matrix
- ABL does not apply dynamic Z height adjustment when bridging
- ABL does apply Z height adjust for infill moves

When the machine receives the infill movement, it executes with slicer defined (feature) adjustments for infill movement, although in this case we are technically bridging.  The curve in question is ~30degrees... but the slicer artifact results in an actual angle of 90degrees.  In normal cases, on the current Mentos_RC build this would likely be less of an issue as the z height is static, however, the ABL distro attempts to print the 90degree overhang while also manipulating the Z Height causing major failure in the part.

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

3dGriff, 2017-02-16:
In a move to continue the focus on reducing individual parts I have modified the base to be printed with the mounting brackets.  @BotleHewer thoughts?

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

Closed 2017-02-17.

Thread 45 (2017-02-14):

New MK1 Base Side must be adjusted for 42mm NEMA 17

3dGriff, 2017-02-14:
Add clearance to MK1 Base Side

3dGriff, 2017-03-02:
Adjusted and added in commit 33ca6f260559425dc5b35a61ca9033ec81d6ee80

Part tested for clearance.

Closed 2017-03-02.

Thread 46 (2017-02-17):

Verify V2 Control Board Commit

3dGriff, 2017-02-17:
Verifying .v2 control board _will update when complete_ see issue #44 for background

3dGriff, 2017-02-18:
@BotleHewer have you conducted a test print print of the V2 cover in PET?  I'm trying to track identify if an issue exists.

BotleHewer, 2017-02-18:
@3dGriff Cover v2 print test done.
No major issues. Recommend printing with support for finish quality on Filleted edge. but possibly not necessary with settings and calibration.
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

3dGriff, 2017-02-19:
I've gotten side tracked in the code, @BotleHewer can you take a look at the R2 base in commit d5df66964ae1c2c9afdfe23c2159d26bf9bfe89c and modify your base to include mounts as well.

BotleHewer, 2017-02-19:
@3dGriff in assembling my test of the SnapMountable version of the board case & mounts, the cover port hole for the endstop wires was identified as misslocated. A new version(v3) has been up replaced on the repo, but has not yet been printed an/or verified.

While functionally working as planned minor improvements to the snap mounts also planed.

3dGriff, 2017-02-22:
Thanks @BotleHewer can you upload the images of your test.  Also, have you made any progress on the base that includes the mounts?

BotleHewer, 2017-02-28:
Perm-mountable version of base uploaded. Unable to test as my printer is down due to nozzle clog.

3dGriff, 2017-02-28:
@BotleHewer got it, I'll run it tonight.

3dGriff, 2017-03-01:
@BotleHewer After using the case on one of the dev machines I think it needs a latch of some kind.  Thoughts?

3dGriff, 2017-03-01:
@BotleHewer Tested base, looks fine.

I suggest the mount to Y Carriage 2020 fastener location should be more accessible, the current design makes turning the M4 tricky.

BotleHewer, 2017-03-07:
Updated for Wrench access on Y mount
https://github.com/Hooklet3d/OdinOne/blob/Mentos_RC/Parts/OdinOne/Mods/Controller_Mount/BrainBoardBase_permMountable.v3.stl

BotleHewer, 2017-03-21:
@3dGriff I have an idea of how to add a simple "latch". more of a snap tab which should effect material cost & print time only slightly. Working on design now will have prototype design later today.

BotleHewer, 2017-03-21:
@3dGriff @J-Skepp
Just noticed an issue with the Controller Board cover in current iteration that will make it not fit controller board base properly. will fix while working on adding the snap/latch system.

Current cover on github should not be printed.

BotleHewer, 2017-03-21:
@3dGriff Updated files in MC repo of updated controller board case system. Fixxes applied as well as snap latch added.

Needs Verification

3dGriff, 2017-03-22:
@BotleHewer got it thanks.

3dGriff, 2017-03-25:
@BotleHewer after putting together the last kit I noticed some weakness in the mount points (to the machine) on the base.  Also, I had to 'shim' the mount point to get the M4 for lock properly into the hammer.

Any thoughts on how we could make this stronger.  My thoughts are that the mount points could just be made thicker.

3dGriff, 2017-04-06:
as mentioned in issue #61 the stepper drivers do seem to be causing issues with this lid.  I think its best to move forward with adding space above the drivers.  Seeing the issue in kit testing at the moment.

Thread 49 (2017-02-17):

Publish new MK1 parts files to RC branch

3dGriff, 2017-02-17:
MK1 .STL file upload and verify

3dGriff, 2017-03-02:
Frame parts uploaded, testing in progress.  Will upload movement parts tonight.

3dGriff, 2017-03-02:
@BotleHewer Movement parts uploaded, haven't been verified.  See commit 1d807f1ef57e300578d9627bf163a5b4cb9b5bb0 for details.

BotleHewer, 2017-03-21:
@3dGriff working on s3d verification now.

BotleHewer, 2017-03-21:
Note: Controller_permMountable.v2.stl not verified at this time because it is being reworked to add snap/latch to lid

Report: Part Slicer check
All parts sliced with
PETG $19/1kg
0.2mm Layer Height
3 perimeters
4 top
4 bottom
35% infill
Def Print Speed: 3200 mm/min (53mm/sec)
3 skirt outlines with 4mm offset

---

BedSkate_Set_MK1.stl

supports needed: possibly
Visual inspection: Cleared
Est material cost/print time: $0.98 / 3.5hrs

UniCap_Idle_MK1.stl

supports needed: yes
Visual inspection: Cleared
Est material cost/print time: $3.23 / 11.25hrs

UniCap_NEMA_MK1.stl

supports needed: yes
Visual inspection: Cleared
Est material cost/print time: $3.17 / 11hrs

XIdle_Back_MK1.stl

supports needed: yes
Visual inspection: Cleared
Est material cost/print time: $0.31 / 1.25hrs

XSkate_MK1.stl

supports needed: no
Visual inspection: Cleared
Est material cost/print time: $0.69 / 2.5hrs

YIdle_Mount_MK1.stl

supports needed: no
Visual inspection: Cleared
Est material cost/print time: $0.19 / 1hrs

3dGriff, 2017-05-01:
Issue closed

Closed 2017-05-01.

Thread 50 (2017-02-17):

Frame parts upload and commit

3dGriff, 2017-02-17:
Currently verifying and uploading frame related parts as per issue/project item #49

3dGriff, 2017-02-17:
@BotleHewer please verify the parts committed to #47 RC within slicer.  Let me know if you run into any issues.

3dGriff, 2017-02-17:
@BotleHewer thanks

Closed 2017-02-17.

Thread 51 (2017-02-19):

Extruder Wire Length

BotleHewer, 2017-02-19:
Length of Nema extruder wires need to be increased by at least 25cm to accommodate moving main board off PSU.

See img for reference.
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

Consider moving extruder assembly wire path to either next to(or attached to) Y endstop mount. Or possibly to left cross beam end (similar to pre-mentos Odin One build).

3dGriff, 2017-02-19:
#46

3dGriff, 2017-03-25:
The initial cable lengths for the X, Y, Z axis are 70cm.  The length for the Extruder cable is 100cm providing full vertical movement.

Closed 2017-03-25.

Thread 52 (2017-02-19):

Verify New Upper 90's

3dGriff, 2017-02-19:
Commit 33ca6f260559425dc5b35a61ca9033ec81d6ee80 includes upper 90's for the rear of the machine, these have not been tested on any level.  Verification is needed...

The right upper 90 now includes a simple guide for the PTFE tube, please add to current builds and test for any potential issues.

Thanks.

3dGriff, 2017-03-02:
@BotleHewer bump on this, have you looked at these?

3dGriff, 2017-03-07:
Tested, Verified.  Closing

Closed 2017-03-07.

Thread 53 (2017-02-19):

PSU Spool Mount design.

BotleHewer, 2017-02-19:
Design a spool mount mod for the psu for MK1 design.
This should/could include mounting of PTFE tube intake to top cross beam.

This will not necessarily ship with production, but will be available on github mod collections.

** Note to @BotleHewer merge current PTFE tube PSU mount, with current 3d printed table mount(or something similar)

3dGriff, 2017-03-07:
@BotleHewer any progress on this?

BotleHewer, 2017-03-07:
@3dGriff not at this time. current system working ok.

3dGriff, 2017-03-19:
Closed due to inactivity

Closed 2017-03-19.

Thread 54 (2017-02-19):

Temperature/Heating issue

3dGriff, 2017-02-19:
We are noticing an issue with the PID remaining stable as it approaches and reaches it's target temperature.

In some cases this fluctuation prevents the HYSTERESIS function in marlin from beginning the print, or in other words the printer is not able to verify a stable temperature during the thermal check, thus it does not begin.

My replication of this issue has not been able to connect it to anything within the firmware itself, I will be doing some repeatability testes to verify a few things.

I would like to see results from the Mentos_RC branch for the following.

- verify you are using a valid PID
- run: M303 E0 S200 C5 a total of five times and report all five PID outputs

I want to see if we generate a constant result, I'm trying to link this to a root issue, I'm leaning in the direction of hardware, however, I'm still not certain.

I will report my findings and results as they come in.

3dGriff, 2017-03-25:
Closing issue due to inactivity.  Issue resolved by adjusting both hysteresis and thermistor settings.  A hardware issue was found on only one machine.  Will reopen if it becomes an issue in the future.

Closed 2017-03-25.

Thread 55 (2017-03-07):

Draft Fan Guard Dim Incorrect

3dGriff, 2017-03-07:
Scale of fan guard for draft fan is not correct 75c33fd2c480100437d8873ee7598ae6496d191b . Working issue now

3dGriff, 2017-03-20:
These should be relatively close at this point but it needs verification.

J-Skepp, 2017-03-21:
Fan guard 75c33fd has been printed and verified.

3dGriff, 2017-03-21:
@J-Skepp I noticed it still might be too large, did you also test for fit?  Could be wrong.

3dGriff, 2017-03-28:
closed due to inactivity

Closed 2017-03-28.

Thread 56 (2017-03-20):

Figured I'd start off by doing it wrong

J-Skepp, 2017-03-20:
I'm sure this is the wrong place to post this, but I don't believe the active cooling assembly has been added to the list of models.  I have a broken part that needs to be printed.

Closed 2017-03-21.

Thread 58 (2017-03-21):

Blower Fan Duct not solid

BotleHewer, 2017-03-21:
Fan duct design for blower fan (https://github.com/Hooklet3d/OdinOne/blob/Mentos_RC/Parts/OdinOne/Mods/Active_Cooling/MK8_DraftCooler/Fan_Duct_DraftCoolerMK8.stl) is not solid. Causing issues in S3d where it tries to bridge a solid floor mid way up part. see screen cap.
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

Attempt to fix by making solid in Meshmixer.

BotleHewer, 2017-03-21:
Part run through make solid and commuted to MC #3a03137.

Slicing Verified in S3D. Print test to follow

3dGriff, 2017-03-21:
@BotleHewer I just added a duct with an altered angle, check out the file in commit 92b1064c5126dc025e64072dadda26c2cc1ede12 I think it's best to just fix it now if you could.

Be aware of the slight indentation at the top of the duct (the part that attaches to the fan) this was added to provide a tighter fit and make sure the duct does not fall off during printing.

BotleHewer, 2017-03-21:
@3dGriff  It appears above issues are not present in latest version of duct.

S3D verified.  Will be printing shortly.

Issue can be closed IMO

3dGriff, 2017-03-22:
@BotleHewer that's good to know, as a heads up your nozzle may be slightly higher or lower than the current machine, verify dimension and positioning with that in mind.

Closed 2017-03-28.

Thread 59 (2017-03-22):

Sainsmart Mockup

J-Skepp, 2017-03-22:
I'm throwing this mock-up of the 2in1 up just for reference.  Don't know where it should go.
It can use more detail or get deleted.  Either way.
Throw the virtual board  in the virtual case and see if the virtual screw holes line up.
G'night

3dGriff, 2017-03-23:
@J-Skepp Awesome, I'll make a directory called 'jigs', submit the part a s a pull request.

3dGriff, 2017-03-23:
commit 75f33d18618071bb835931385f79e774474fa6b8

Closed 2017-05-01.

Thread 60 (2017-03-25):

Talking points

BotleHewer, 2017-03-25:
A place to collect talking points for Tradeshows, and promotional materials.

BotleHewer, 2017-03-25:
+ Each kit does this before it's boxed
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

+ And gets it's specific calibrated firmware flashed

3dGriff, 2017-03-27:
@BotleHewer please move this issue to the marketing 17 repo.  https://github.com/Hooklet3d/Marketing_17

This should be reserved for issues specific to the Odin One from a development standpoint.

Thanks.

BotleHewer, 2017-03-28:
@3dGriff issue recreated in marketing.
ok to close

3dGriff, 2017-04-06:
Moved and closed

Closed 2017-04-06.

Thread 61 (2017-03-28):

Stepper Heating / Board Fail Potential

3dGriff, 2017-03-28:
Over the last few weeks I have been working with a user in NC who is doing a retrofit using a SainSmart 2in1 control board.

Last week (March 24, Friday) he reported a failure shown in the attached image.  The failure was a total loss of the board and appears to have impacted the FET regulator used to regulate power to the stepper drivers.

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

_note failure on U8 FET_

Yesterday (March 27, Monday) it was reported internally that elevated heat levels here being observed on the stepper heatsinks.  The design specs for the DRV8825 stepper drivers do not provide any exact numbers for max temps, however, it does state that "this product can get hot enough to burn you long before the chip overheats".

In the past, heat has not been a concern on the stepper drivers, it is possible that the latest firmware build is causing issues.

To ensure this does not happen to our users, I think it wise to develop a study on this issue and try to identify impact and root cause.

@BotleHewer any thoughts much appreciated.

## I Propose the following

### Control Info

- Current ambient temp in room reported
- Current print speed reported
- Current vRef for each driver reported
- Current Movement and Acceleration settings reported

### Testing Process

-Read driver temps prior to printing (5 readings and average)

- Print the CaliCat with the following specs:
-- .2mm height
-- 35mm/s speed

- Read driver temps at 10min intervals during print (5 readings and average)

- Report results

### Finding the source

- I will be making a few modifications to the current firmware and doing the same tests, the goal here is to see if we can ID a causal link.

Any input on this would be great.

3dGriff, 2017-03-28:
## Test 1 Results For Ref

### Conditions

* Abmbient Temp 69F (21C)
* Bed Temp: 60
* Extruder: 200
* Material: PLA
* Speed: 35mm/s

Main Power Input:  12.09v

**Vref**

* E - 0.62v
* X - 0.50v
* Y - 0,59v
* Z - 1.20v

**Print Time: 55:32**

### Raw Temp Readings:

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

### Temp Plot:

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

## Results:

As expected the Z axis is the hottest of the drivers, looking at the data I can rule out the increase in Z movement due to ABL Z correct as the Z Temps do not decrease in any meaningful way prior to the z fade ending.  After 10mm layer height the z corrections are no longer impacting the driver, however, we see no change in the temps at this point.

These temperatures are not alarming in any way.  Although this test was done at a typical high quality print speed I don't see anything significant to suggest major spikes at higher speeds.  I will follow up on this as well.

What's more important is that the U8 FET in question maintained a steady temperature between 38-43c.  This suggests that while operating within the specified voltage ranges we are not causing undue stress to the regulator.

BotleHewer, 2017-03-28:
Here is what Angi reported during a spot check on her bot several hours into a print.

Room Temp   69-70* F
Print speed 84%
    60mm/s support
   45mm/s perimeters
   60mm/s infill

X axis 63*C
Y axis 63*c
Z axis  60*c

Angi-B, 2017-03-28:
second reading 2:45 same print
X axis 57*C
Y axis 76*c
Z axis  64*c
Extruder 49* C

3dGriff, 2017-03-28:
@BotleHewer @Angi-B thanks for this, good so see it seems to be holding at higher speeds.  I think for now we are looking great as far as tolerances.  I wasn't able to find anything explicitly saying what the failure temp is on the DRV8825's but based on other systems I might estimate it in the mid 100c's... For now we can move forward without any active cooling on the board.  The Sainsmart was designed with high heat tolerances in mind.

### Consideration and further reading.

The new latest firmware defines a minimum step pulse of 4_us_ this was done to accommodate the mininimum pulse width of 1.9_us_ on the DRV8825 whereas the standard A4988 drivers utilize a minimum pulse width of 1_us_.

I will move forward in testing the effects of reducing this to 2_us_ in order to more closely match the driver's specs.

@BotleHewer I am interested to see your results on this test as your machine is still utilizing the default step width of 1_us_.

### References

If you wish to know more about this check these links out...

https://www.pololu.com/product/2133

https://en.wikipedia.org/wiki/Pulse-width_modulation

BotleHewer, 2017-03-28:
@3dGriff  I don't own a laser therm. I'm due to get one from my father when he sells off his shop but that could be months away. Will see if I can borrow Jeff's for a bit to confirm, but I'm definitely not seeing danger temps at this time

3dGriff, 2017-04-06:
Standing solution seems to be adding space above the drivers on the control board lid.  Carry on in issue #46

3dGriff, 2017-04-06:
Leaving issue open for now, please report any issues that may be related to this one.

3dGriff, 2017-05-01:
Closing due to inactivity

Closed 2017-05-01.

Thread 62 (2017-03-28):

Build directions updates

BotleHewer, 2017-03-28:
Suggestions from Angi:

+ Adding sub-steps labels i.e step 2.1, 2.2 etc. for
+ Photo of the top the wired board for reference
+ List of tools needed: metric alen wrenches, small electronics screwdriver

3dGriff, 2017-04-06:
@BotleHewer subs seem like a good idea, and the tools list should be included as well.

In addition to the photo of the wired board, I think it would be good to add a few reference features to the graphic you have.  This might help a bit when identifying where things need to be plugged in.

The wiring also needs to have the probe wiring added as well.  Info on this can be found here: https://github.com/Hooklet3d/OdinOne/wiki/Z-Probe

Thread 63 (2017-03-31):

Test C-Duct Cooler

BotleHewer, 2017-03-31:
Need to test & Evaluate C-style cooling.
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

BotleHewer, 2017-03-31:
Created and uploaded an alternate version of the Duct that doesn't circle the nozzle as far, but is lighter, smaller, should print without support(at least with active cooling on printer) and gives better visibility on the nozzle.

BotleHewer, 2017-03-31:
What I'm seeing so far is that the angle of the duct still needs adjustment. Cooling is still reducing temp on hotend significantly.

I'm liking the design on V3 better than v2, so I'll attempt to rework the angle of the airflow to miss the nozzle.

3dGriff, 2017-03-31:
Hey just had a machine free up to test on this, I had a question for you.

In slicing it looks like the mesh of the guard doesn't start until layer 3, screenshot included shows tool paths at layer 2.  Is this part of your design?

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

BotleHewer, 2017-03-31:
@3dGriff  that is a glitch in the design. I just looked at it and the hex grid was not flush as I though it was.
Will upload a fixed file in a sec

3dGriff, 2017-04-06:
@BotleHewer as you mentioned the v3 wasn't quite right dimensions wise, I am currently testing the v4 version (current as of this post) it looks good thus for.

Have you thought about or tested moving the duct closer to the nozzle for more direct cooling?

3dGriff, 2017-04-07:
@BotleHewer I ran three test prints, the first with the v4 duct and the last with the existing draft cooler.  The difference can be seen in 90 degree bridging.

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

The last print I did as a comparison, this print has the same slicer settings as the first two and used the existing cooler.

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

From my understanding the A8 style cooler's (and those similar) flaw is that they try to distribute the air over a greater distance thus limiting the overall airflow.  As I mentioned before, I really think the duct needs to be closer to the nozzle.  As it stands I believe the duct is delivering indirect cooling.

I think another thing to consider is that the fan is blowing cool (relative) air into a heated space.  The area around the hot end has a constant updraft—this immediately forces the cooling air upward.  Given the distance and likely diminished airflow, it's unlikely the cooler is making much of a difference.  The ideal cooler needs to consolidate its air to the smallest point possible (ideally just below the nozzle) at no point do we want to cool the entire part or large areas of the part (this can lead to warping issues).  I think it can be done with this duct style it just needs to be worked out.

The design is solid and it looks great, we just need to make it a more functional cooler.  I hope this helps, let me know if you have any questions.

3dGriff, 2017-04-10:
@BotleHewer I was able to resolve this in slicer settings (the bridging issue) however, I am noticing an issue on one machine.  On the machine in question, running the fan over 60% impacts the extruder temp to the point of triggering the thermal protection.

I believe we need to dial in the focus of the airflow.

BotleHewer, 2017-04-10:
@3dGriff As far as the temp issue: the v4 should be angled to alleviate this, as it was an issue with the v3 duct. I'm curious why it's only effecting 1 of your bots, as I'm not having that issue on mine either with the v4 duct.

I'll work on moving the duct closer still to the nozzle, I hope to have a design ready to print later today.

BotleHewer, 2017-04-20:
@3dGriff, @J-Skepp I'm for scrapping the c-duct line of study. Unless objections from anyone else I suggest closing this ticket.
Will open a new ticket for the straight duct currently being dev.

3dGriff, 2017-04-20:
@BotleHewer sounds good, I'll remove and update

3dGriff, 2017-04-20:
Removed in commit baa9d49a1612829164a56751edcb19507baee9b8

Closing issue

Closed 2017-04-20.

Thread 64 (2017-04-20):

Test of New Straight Duct

BotleHewer, 2017-04-20:
Thread for comments & testing of new straight duct system for active cooling.

@3dGriff Currently needing testing of version 3  found in Mentos/OdinOne/Parts/OdinOne/Mods/Active_Cooling/Straight_Duct/

3dGriff, 2017-04-20:
@BotleHewer I'll start testing this in a few.

3dGriff, 2017-05-01:
@BotleHewer Right now it just looks like the vent needs to be moved closer to the nozzle, I'm still seeing area effect cooling.  Generally it's working pretty well, however, I think we can extend overhang quality in the area of ~15 degrees.

BotleHewer, 2017-05-01:
@3dGriff  I have already created a v4 duct designover the weekend that drops the output end of the part by about 1mm & adjusts the output vent angle to be slightly smaller, and to be less downward angled, to reduce spillage and more controlled.

I've preped the file already and is slated to be printed as soon as my Odin is freed up again in a couple hours.
I'm goind to be designing a part to test cooling efficiency at different fan % aswell.
 I intend be testing it no later than tomorrow.

BotleHewer, 2017-05-04:
Just Uploaded V5b to the Mentos Cooling straight duct folder.  I'm having good results with this version.I'd like further testing from others if possible.  I've built a part just for testing the fan at different percentages and will have results of those tests in the next days or so

BotleHewer, 2017-05-04:
First cooing test:  Hatchbox ABS, 0.2 layers, Nozzle 240, bed 85. Fan test range 0-60%. This test used Straight Duct version 5b.

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

My Conclusion so far:
Benefits of cooling for most parts take effect at around 30% fan speeds. And visual improvement of part perimeter & overhang did not significantly improve after 30%.  Current recommendation would be to set base (pre-modified) cooling percent at 35% for ABS printing.

Further testing may provide refined settings for greater bridging results.

BotleHewer, 2017-05-04:
@3dGriff I can also confirm that there was no noticeable difference between quality of print for side facing fan vs side farthest from fan(past nozzle). Not that we were worried about this.

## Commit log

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2016-08-25 Add files via upload
    Added 'base side' STL (fixed)
    [BaseSide_Sprint1.stl]
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2016-08-25 Add files via upload
    Added front and rear base STL files. (fixed)
    [BaseFront_Sprint1.stl, BaseRear_Sprint1.stl]
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2016-08-25 Add files via upload
    Added upper 90 set STL
    [upper90Set_Sprint1.stl]
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2016-08-25 Add files via upload
    Added Z Nema Mounts
    [ZNemaMount_Sprint1.stl]
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2016-08-25 Add files via upload
    Added Z end stop mount.
    [ZEndMount_Sprint1.stl]
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2016-08-25 Add files via upload
    Added Skate STLs
    [Skate_Sprint1.stl, XSkate_Sprint1.stl]
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2016-08-25 Add files via upload
    Added Beamset, YNeam mount and Y end mount...
    [YEndMount_Sprint1.stl, YNemaMount_Sprint1.stl, ZBeamSet_Sprint1.stl]
2016-08-26 Add files via upload
    Added Z Tripper STL
    [ZTripper_Sprint1.stl]
2016-09-03 Fixed Y Tripper Issue
    Adjusted flag for clearance and lowered profile. Issue closed.
    [YTripper_Sprint1.stl]
2016-09-23 Add files via upload
    New X Idle Set to include guide washers.
    [XIdleSet.stl]
2016-09-28 Add files via upload
    Raised NEMA base for better support
    [BaseSide1.0.stl]
2016-09-28 Delete ZNemaMount_Sprint1.stl
    Removed to update..
    [ZNemaMount_Sprint1.stl]
2016-09-28 Add files via upload
    Added depression to face of skate mount to support the use of M4 Bolts in connecting the the Z Skates. Tested @ .02mm dimensional accuracy with smooth moment.
    [ZSkateMountSet.stl]
2016-09-29 Delete YNemaMount_Sprint1.stl
    Removed for update.
    [YNemaMount_Sprint1.stl]
2016-09-29 Add files via upload
    Adjusted for 40mm NEMA...
    [YNemaMount1.0.stl]
2016-09-29 Delete ZBeamSet_Sprint1.stl
    Redundant Part
    [ZBeamSet_Sprint1.stl]
2016-09-29 Delete YTripper_Sprint1.stl
    removed for update
    [YTripper_Sprint1.stl]
2016-09-29 Add files via upload
    File Fixed
    [YTripper1.0.stl]
2016-09-29 Delete ZEndMount_Sprint1.stl
    Removed for update
    [ZEndMount_Sprint1.stl]
2016-09-29 Delete YNemaMount1.0.stl
    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
    [YNemaMount1.0.stl]
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2016-09-29 Add files via upload
    Added Belt Mount
    [YBeltMount_Sprint1.stl]
2016-09-30 Delete BaseRear_Sprint1.stl
    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
    [BaseRear_Sprint1.stl]
2016-09-30 Add files via upload
    Added hex tabs for adhesion
    [BaseRear_Sprint1.stl]
2016-09-30 Delete ZSkate1.0.stl
    Removed to add fixed version.
    [ZSkate1.0.stl]
2016-09-30 Add files via upload
    Added Fixed Model
    [ZLinearSkate1.0.stl]
2016-10-02 Add files via upload
    Added wire channel
    [BaseRear1.0.stl]
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2016-10-05 Delete BaseSide1.0.stl
    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
    [BaseSide1.0.stl]
2016-10-05 Add files via upload
    One of the hex tabs was not flush to the bed. Fixed for better adhesion.
    [BaseSide_Sprint1.stl]
2016-10-05 Delete BaseSide_Sprint1.stl
    Removed For update
    [BaseSide_Sprint1.stl]
2016-10-05 Add files via upload
    updated.
    [BaseSide_Sprint.stl]
2016-10-05 Add files via upload
    Odin webcam mounting system upload.
    [arm_thing_fixed.stl, c270mount.ForSystem.v3_fixed.stl, odin_front_adapter_fixed.stl]
2016-10-05 Delete ChainX1.stl
    Moving to sub folder to be next to other versions
    [ChainX1.stl]
2016-10-05 Add files via upload
    Modified with notch for 3DPrintable spring. Spring also uploaded.
    [ChainSpring_x1.stl, Chain_notched_x1.stl]
2016-10-06 Add files via upload
    Alternate version with Hooklet Logo.
    [upper90set_branded.stl]
2016-10-08 Delete 2020-Xchain_suport.stl
    Removed for Update
    [2020-Xchain_suport.stl]
2016-10-08 Delete xbeltextender_chain_adapter.stl
    Removed for refinement
    [xbeltextender_chain_adapter.stl]
2016-10-11 Delete LCDFront1.0.stl
    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
    [LCDFront1.0.stl]
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2016-10-11 Add files via upload
    Patched version of LCD face & Branded Version
    [LCDFront1.0_.stl, LCDFront1.0_branded.stl]
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2016-10-11 Add files via upload
    Updated for name clarity
    [BedSkate_Sprint1.stl]
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2016-10-14 Add files via upload
    Added guide to help keep chain in place
    [xbeltextender_chain_adapter.stl]
2016-10-14 Add files via upload
    Version with filament guide
    [xbeltextender_chain_adapter_fialmentguide.stl]
2016-10-14 Add files via upload
    Fixed file to address slicing errors
    [XidlerSet_1.0.stl]
2016-10-14 Delete XidlerSet_1.0.stl
    removed for naming convention fix
    [XidlerSet_1.0.stl]
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2016-10-22 Add files via upload
    Nema side of mount made a bit thicker for better strength.
    [MK8_1.0_reinforced_noclamps.stl]
2016-10-22 Delete MK8_1.0_reinforced_noclamps.stl
    wrong file.
    [MK8_1.0_reinforced_noclamps.stl]
2016-10-22 Add files via upload
    Correct file with clamps included.
    [MK8_1.0_reinforced.stl]
2016-11-06 Add files via upload
    Modded to hold replacement dupont cable better
    [YEndMount_1.1.stl]
2016-11-07 Add files via upload
    Modded to keep dupont cable in place better
    [ZEndMount_1.1.stl]
2016-11-07 Add files via upload
    modded for dupont cable keeper
    [XEndMount_1.1.stl]
2016-11-07 Delete ZEndMount_1.1.stl
    not yet tested. uploaded wrong file
    [ZEndMount_1.1.stl]
2016-11-07 Add files via upload
    Updated to hold dupont better, & move hammer nut to front of 2020
    [ZEndMount_1.1.stl]
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2017-02-12 Prototypes
    Uploading main boar case & mounting prototypes
    [BrainBoardCover_branded.stl, BrainBoard_Xmount.stl, BrainBoard_Ymount.stl]
2017-02-16 Uploaded Updated board cover
    re-worked board cover for slicing per comments in issue #44
    [BrainBoardCover.v2.stl]
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2017-02-16 Uploaded new base and Snap Fit mounting mods
    [BrainBoard_XSnapMount.stl, BrainBoard_YsnapMount.stl]
2017-02-17 MK1 Parts Update - FRAME
    Commit for frame parts:
    Removed sprint and / .1 generation parts and replaced with MK1 gen.
    Parts should be verified for slicing at the very least. Issues should
    be reported and resolved.
    [BaseFront_Sprint1.stl, BaseRear1.0.stl, BaseSide_Sprint.stl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]
2017-02-19 Small Fixes and upload
    I added my rework including the mounts for reference.
    [Control_Base_R2.stl, ControllerBoard_Cover.v2.stl, Controller_XSnapMount.stl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]
2017-02-19 Updated for fix
    Fixed location of optical sensor wire port.
    [BrainBoardCover.v3.stl]
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2017-03-07 'Draft Cooler" MK8 Active Cooler
    Uploaded new ‘Draft Cooler’ active cooling system for the MK8 Extruder
    set.
    [Fan_Duct_DraftCoolerMK8.stl, Fan_Guard_DraftCoolerMK8.stl, Fan_Mount_DraftCoolerMK8.stl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]
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2017-03-21 Docs and Draft Cooler Push
    Updated altered duct file, rough BOM and crossbeam documentation
    [BOM_working.xlsx, Fan_Duct_DraftCoolerMK8.stl]
2017-03-21 Fixed/modified
    Updated for fixes, and to add snap/latch to cover.
    [ControllerBoardCover.v4.stl, ControllerBoard_XSnapMount.stl, ControllerBoard_YsnapMount.stl]
2017-03-22 MK8 Mount with Auto Probe
    Part commit for MK8_MK1 mount.
    [MK8_1.0.stl, MK8_1.0_reinforced.stl, MK8_Mount_MK1.stl]
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2017-03-27 Doc fix/new addition
    Fixed an error in the leveling procedure and uploaded temp issue test
    report and basic Z Probe wiring overview.
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2017-04-01 Pushed new upper 90 REAR
    Upper 90 rear set with PTFE slots on both sides
    [Upper90_Rear_SET_MK1.stl]
2017-04-06 Added new parts
    Added the following:
    *cable tags for kit wiring
    *2020 cable guide
    * PSU Mounts fixed and separated
    [Mount_PSU_SET_MK1.stl, PSUMOunt_R_MK1.stl, PSUMount_L_MK1.stl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]
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2017-04-20 Moved File
    Moved fan guard (Skepp) to Mods/Guards/
    [FanGuard_Hex.stl]
2017-04-20 Add files via upload
    mounting & guards for active cooling
    [MK1.1BlowerMod_STRAIGHT.V3.stl, MK1.1BlowerMod_mount_v2.stl]
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2017-05-19 Mercury Rework 1
    Reworked the following items:
    *MK8 Mount
    *Bed Belt Mount
    *Unicap NEMA
    *Unicap Idle
    *X Idle Face
    *Y Idle Mount
    [MK8_Mount_MK1.stl, Mount_Bed_Belt_MK1.stl, Mount_Belt_Bed_MK1.stl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]
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
